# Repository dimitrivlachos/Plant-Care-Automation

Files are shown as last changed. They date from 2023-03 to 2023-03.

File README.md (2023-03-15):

# Plant Care Automation
ESP8266 microcontroller based, automated plant care project for ```CM3040 - Physical Computing and Internet of Things``` University of London.

To build out this system, I decided I would have a server-client type relationship between the controllers. The ```Base Station``` would be the server/host/controller of the entire system and it would serve multiple ```Plant Monitoring Stations```, which were the clients. I only built one example of each, but the general concept should be near infinitely scalable. These nodes communicate through REST-based HTTP requests, transferring JSON data as requested.

## Project design and demonstration video
IoT Demo Video (https://www.youtube.com/watch?v=c-YxRt0L1Ww)

## Nodes
The ```Base Station``` would monitor and display ambient environmental factors, as well as the water reservoir for the plants, checking in with each monitor node and issuing commands, such as to water the plant, turn on a light or open the greenhouse for fresh air. This node would be plugged into a mains power source and be somewhere prominent where it can display information.

The ```Plant Monitoring Station```, on the other hand, would be attached to each plant/greenhouse container. It would monitor the direct conditions affecting the plant, such as the soil moisture, temperature and humidity. It would also control the pump, servo and lights that water, open and illuminate the plant, based on commands issued from the base station.

---

# Breakdown of circuits
## Base Station

### Input / Sensors
* BMP280 - Temperature, humidity and barometric pressure sensor.
* BH1750 - Ambient light sensor.
* HCSR04 - Ultrasonic distance sensor.
* Push button - Used to manually trigger watering.

### Output / Actuators
* SSD1306 - 128x64 OLED display.
* Integrated LED - Used to indicate when the system is active on the network.

### JSON Data
The base station node sends JSON data in the following format:
```json
{
  "Content-Type": "application/json",
  "Status": 200,
  "Readings": {
    "temperature": 21.18000031,
    "humidity": 64.43847656,
    "pressure": 1017.714844,
    "lux": 49.16666412,
    "fill_percent": 100
  }
}
```

### Operation
The base station node constantly checks its sensors and updates its readings, displaying them on the OLED display. If an HTTP request is made to the base station, depending on the request, it will respond with either an HTML web dashboard or a JSON object containing its sensor readings.

The web page contains code that regularly sends an HTTP request to the base station, to get updated sensor readings in the form of a JSON. It then updates the web page with the new readings.

The physical push button is duplicated on the web page, this can be pressed to manually trigger watering. When the button is pressed, the base station will send an HTTP command to the plant monitoring stations to water the plants.

The base station also has a built-in LED that is used to indicate when the system is active on the network. It flashes three times when a request is made for the web page, and it flashes twice when a request is made for JSON data instead. It also flashes four times when initialising the BME280 sensor on startup.

The location of the text on the OLED display regularly shifts in order to prevent burn-in.

The ultrasonic distance sensor is used to check the water level in the reservoir. It is mounted above the water in the resevoir that each plant stations' pump draws from. This information can be checked on the web page.

The base station checks in with each of the plant monitoring stations regularly, it sends an HTTP request for a JSON file containing the status of each node.

It then processes the JSON data and decides whether to issue a command to the plant monitoring station. The commands are as follows:
1. If the pump is **not** running, it will check if the soil moisture is below a certain threshold. If it is, it will send an HTTP command to the plant monitoring station to water the plant.
2. If the lid (controlled by the servo) is **closed**, it will check if the temperature inside the greenhouse is too hot. If it is, it compares it with the outside, ambient temperature. If the greenhouse is hotter, it will send an HTTP command to the plant monitoring station to open the lid.
3. If the lid (controlled by the servo) is **open**, it will check if the temperature inside the greenhouse is too cold. If it is, it will send an HTTP command to the plant monitoring station to close the lid.
4. If the light is **off**, it will check if the ambient light is too low. If it is, it will send an HTTP command to the plant monitoring station to turn the plant light on.
5. If the light is **on**, it will check if the ambient light is adequate. If it is, it will send an HTTP command to the plant monitoring station to turn the plant light off.

### Circuit Diagram
* The **BME280** and **BH1750** sensors are connected to the ESP8266 via I2C, along with the **SSD1306** display. This is using the default I2C pins, SCL on pin D1 and SDA on pin D2.
* The **HCSR04** ultrasonic distance sensor is connected to the ESP8266 via the default pins, trigger on pin D6 and echo on pin D7.
* The push button is connected to pin D5 and has a pull-down resistor to ground.
* The integrated LED is internally connected to pin D4 (and the signal is inverted).

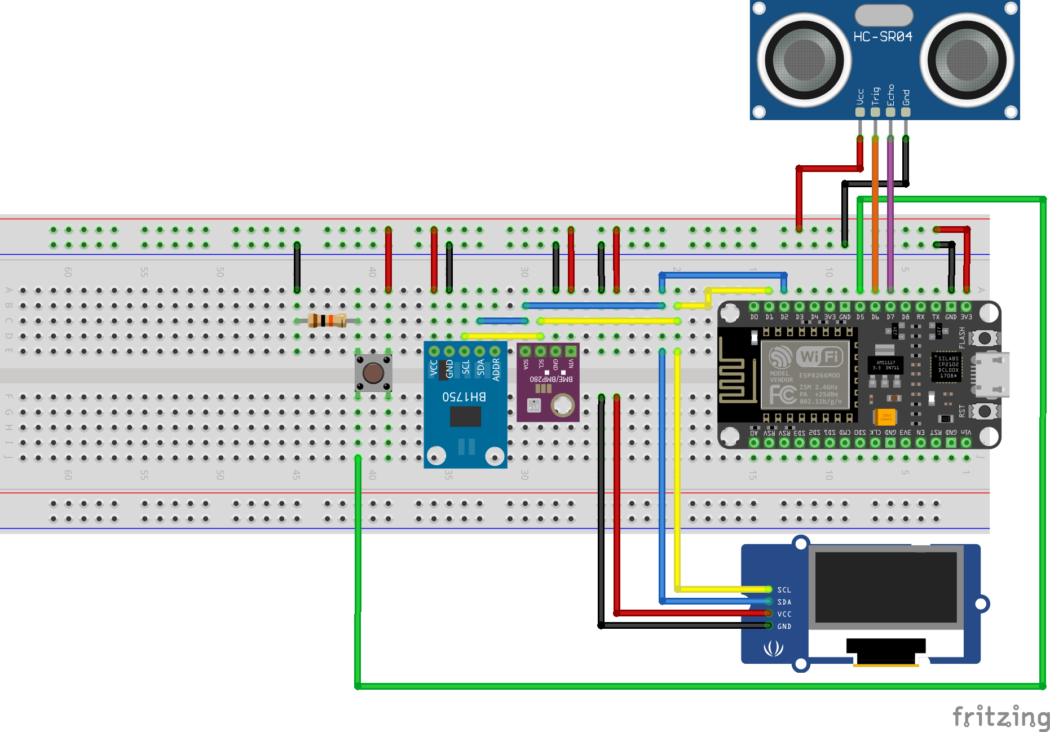
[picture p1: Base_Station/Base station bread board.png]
Base station breadboard diagram


### Web Interface
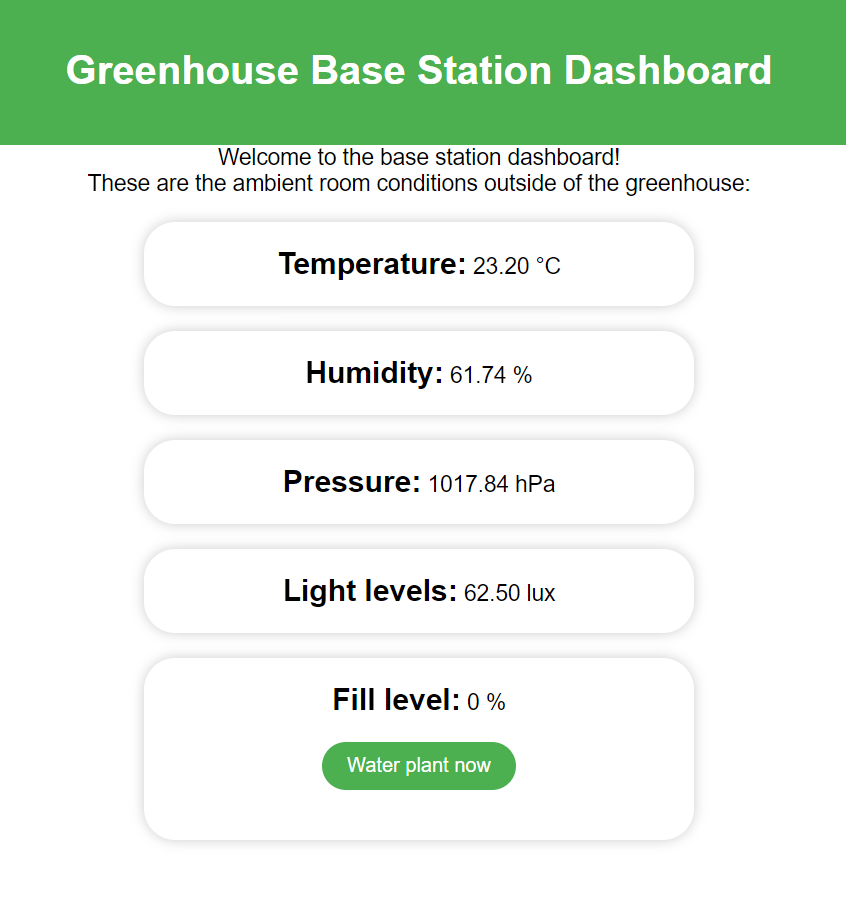
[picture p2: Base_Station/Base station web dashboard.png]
Base station web interface screenshot


## Plant Monitoring Station

### Input / Sensors
* DHT11 - Temperature and humidity sensor.
* Capacitive soil moisture sensor.

### Output / Actuators
* Servo - Used to open and close the lid of the greenhouse.
* Relay - Used to control the power to the pump.
* Pump - Used to water the plant.
* LED - Used to illuminate the plant.
* Integrated LED - Used to indicate when the system is active on the network.

### JSON Data
The plant monitoring station node sends JSON data in the following format:
```json
{
  "Content-Type": "application/json",
  "Status": 200,
  "Readings": {
    "soil_moisture_percent": 97,
    "temperature": 21,
    "humidity": 60
  },
  "States": {
    "servo_state": false,
    "pump_state": false,
    "light_state": true
  }
}
```

## Operation
The plant monitoring station node constantly checks its sensors and updates its readings. If an HTTP request is made to the plant monitoring station, depending on the request, it will respond with either an HTML web dashboard or a JSON object containing its sensor readings.

The web page contains code that regularly sends an HTTP request to the plant monitoring station, to get updated sensor readings in the form of a JSON. It then updates the web page with the new readings.

The web page includes a 'Water plant now' button, this can be pressed to manually trigger watering. When the button is pressed, the base station will run its ```water_plant()``` function manually, allowing users to trigger individual nodes to water.

The plant monitoring station also has a built-in LED that is used to indicate when the system is active on the network. It flashes three times when a request is made for the web page, and it flashes twice when a request is made for JSON data instead.

The plant monitoring station does not act on its own, it only responds to HTTP commands from the base station, such as:

* Request sensor readings - This is done by sending a JSON object containing the sensor readings.
* Request index page - This is done by sending an HTML web page.
* Water the plant - This is done by turning on the pump for a set amount of time before turning it off again.
* Open the lid - This is done by rotating the servo to a set angle.
* Close the lid - This is done by rotating the servo to its original angle.
* Turn the light on - This is done by turning on the LED pin. (For a more powerful LED, this can be replaced with a relay to control a mains powered light.)
* Turn the light off - This is done by turning off the LED pin.

### Circuit Diagram
* The **DHT11** sensor is connected to the ESP8266 via the D5 pin.
* The **capacitive soil moisture sensor** is connected to the ESP8266 via the A0 pin (This prevents us from being able to measure battery percentage).
* The **servo** is connected to the ESP8266 via the D6 pin.
* The **relay** (and **pump**) are connected to the ESP8266 via the D7 pin.
* The **LED** is connected to the ESP8266 via the D1 pin.

In this diagram, the entire circuit is powered by a battery pack. However, this is only representative of the solar power circuit intended to power it, as its exact operation is not important to this project. For the sake of environmental friendliness and ease of installation, these nodes are intended to be solar powered and contain a battery pack to store the energy.

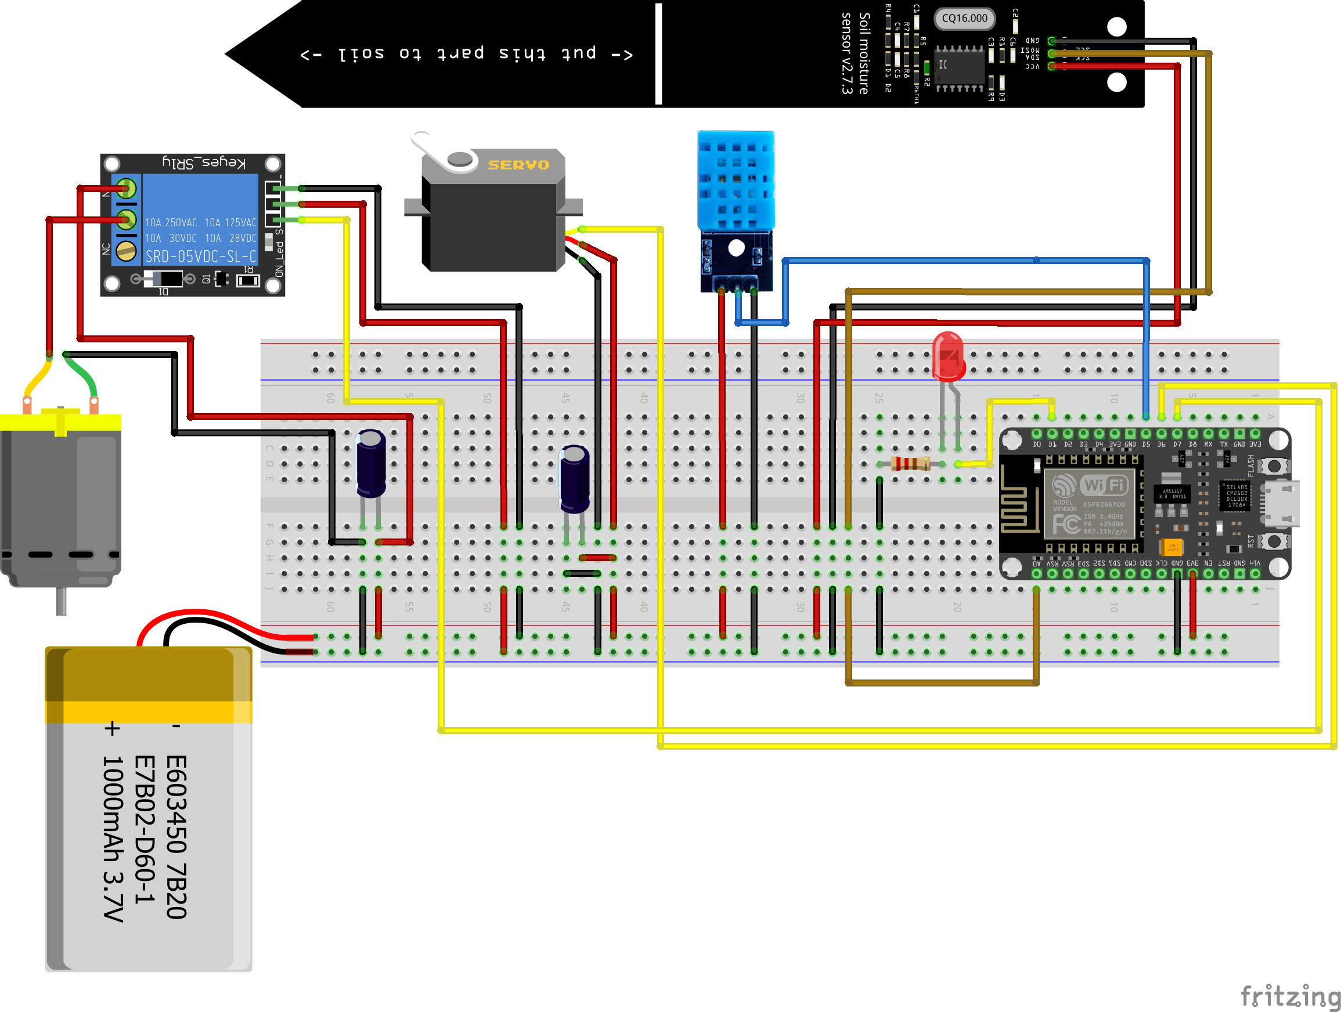
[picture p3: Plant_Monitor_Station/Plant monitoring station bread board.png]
Plant monitoring station breadboard diagram


### Web Interface
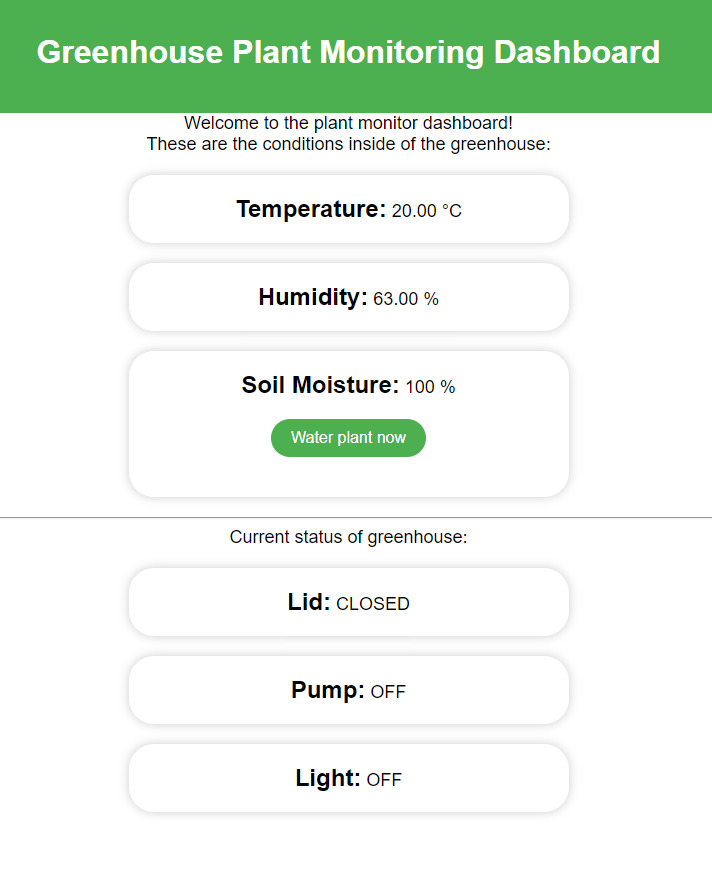
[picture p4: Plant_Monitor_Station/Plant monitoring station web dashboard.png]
Plant monitoring station web interface screenshot


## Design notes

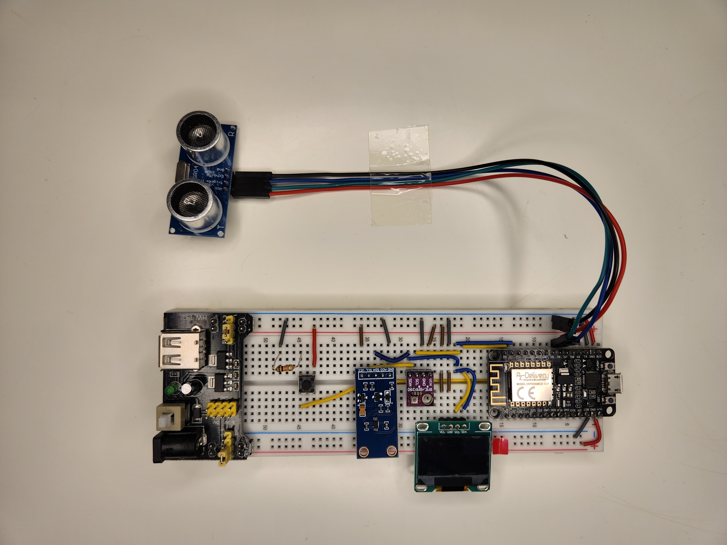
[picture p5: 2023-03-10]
Base_Station/Base station prototype breadboard.jpg

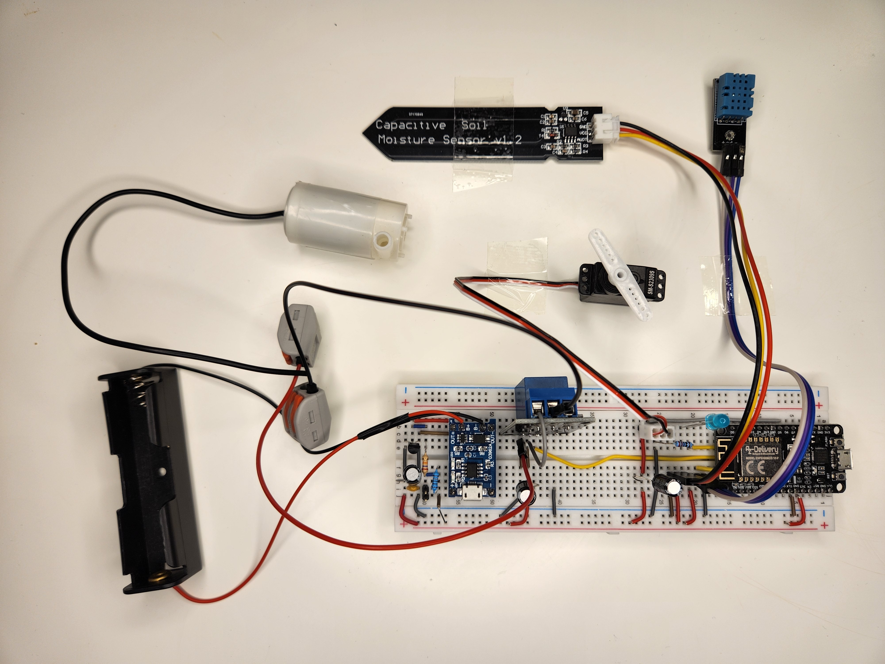
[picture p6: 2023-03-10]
Plant_Monitor_Station/Plant monitoring station prototype breadboard.jpg

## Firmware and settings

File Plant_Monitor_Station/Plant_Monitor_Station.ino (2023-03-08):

/*
 *  Code by:  Dimitrios Vlachos
 *            dimitri.j.vlachos@gmail.com
 *
 *  Adapted from:
 *            UoL Lectures
 *            https://randomnerdtutorials.com/esp8266-pinout-reference-gpios/
 *            https://makersportal.com/blog/2020/5/26/capacitive-soil-moisture-calibration-with-arduino
 *            https://randomnerdtutorials.com/esp8266-nodemcu-http-get-post-arduino/
 *            https://arduinojson.org/
 *
 */

#include <Adafruit_Sensor.h>
#include <Adafruit_BME280.h>
#include <Arduino_JSON.h>
#include "DHT.h"
#include <Servo.h>
#include <TaskScheduler.h>

/* * * * * * * * * * * * * * * */
#pragma region Networking
#include <ESP8266WiFi.h>
#include <ESP8266WebServer.h>
#include <ESP8266HTTPClient.h>
#include <ArduinoJson.h>

// For OTA
#include <WiFiUdp.h>
#include <ArduinoOTA.h>

// Allocate the JSON document
// Allows to allocated memory to the document dynamically.
DynamicJsonDocument doc(1024);

// Set the PORT for the web server
ESP8266WebServer server(80);

// The WiFi details
const char* ssid = "REPLACE_WITH_YOUR_SSID";
const char* password = "REPLACE_WITH_YOUR_PASSWORD";
#pragma endregion
/* * * * * * * * * * * * * * * */

Scheduler userScheduler;

/* * * * * * * * * * * * * * * */
// Function prototypes
/**
 * Updates global sensor reading variables with
 * new information from the sensors
 */
void updateReadings();
void blinkOn();
/*
 * blink the onboard LED
 *
 * @param blinks Number of times to blink the LED
 * @param interval Delay between blinks
 */
void blinkLED(int blinks, long interval = TASK_SECOND / 10);  // Prototype for default parameter values
void stopWatering();

/* * * * * * * * * * * * * * * */
// Create tasks
Task taskUpdateReadings(TASK_SECOND * 5, TASK_FOREVER, &updateReadings);
Task taskLedBlink(TASK_SECOND / 2, 4, &blinkOn);
Task taskStopWateringTimer(TASK_SECOND * 5, TASK_FOREVER, &stopWatering);

/* * * * * * * * * * * * * * * */
// Pin declarations
const int light_pin = D1;
const int led_pin = D4;
const int dht_pin = D5;
const int servo_pin = D6;
const int pump_pin = D7;
const int soil_pin = A0;

// Values to calibrate for soil moisture sensor
const int air_value = 620;
const int water_value = 310;

// Base node address
const String baseAddress = "http://192.168.0.201";

/* * * * * * * * * * * * * * * */
// Sensor declarations
// Initialise the components

DHT dht(dht_pin, DHT11);
Servo serv;

/* * * * * * * * * * * * * * * */
// Dynamic global variables

int soil_moisture_percent;
int temperature;
int humidity;

// Boolean to check open/close status of servo
bool isServoOpen = false;
bool isPumping = false;
bool light = false;

void setup() {
  // Start serial communication
  Serial.begin(115200);
  // Set the light relay pin mode
  pinMode(light_pin, OUTPUT);
  // Set led pin mode (integrated LED)
  pinMode(led_pin, OUTPUT);
  // Set pump pin mode
  pinMode(pump_pin, OUTPUT);

  // Initialise sensor
  dht.begin();
  // Initialise actuator
  serv.attach(servo_pin);
  // Populate initial sensor data
  updateReadings();

#pragma region WiFi Setup
  //Connect to the WiFi network
  WiFi.begin(ssid, password);

  // Wait for connection
  while (WiFi.status() != WL_CONNECTED) {
    delay(500);
    Serial.println("Waiting to connect...");
  }

#pragma region OTA Setup
  // Port defaults to 8266
  // ArduinoOTA.setPort(8266);

  // Hostname defaults to esp8266-[ChipID]
  ArduinoOTA.setHostname("Plant Monitor Station");

  // No authentication by default
  ArduinoOTA.setPassword("admin");

  // Password can be set with it's md5 value as well
  // MD5(admin) = 21232f297a57a5a743894a0e4a801fc3
  // ArduinoOTA.setPasswordHash("21232f297a57a5a743894a0e4a801fc3");

  ArduinoOTA.onStart([]() {
    String type;
    if (ArduinoOTA.getCommand() == U_FLASH) {
      type = "sketch";
    } else {  // U_FS
      type = "filesystem";
    }

    // NOTE: if updating FS this would be the place to unmount FS using FS.end()
    Serial.println("Start updating " + type);
  });
  ArduinoOTA.onEnd([]() {
    Serial.println("\nEnd");
  });
  ArduinoOTA.onProgress([](unsigned int progress, unsigned int total) {
    Serial.printf("Progress: %u%%\r", (progress / (total / 100)));
  });
  ArduinoOTA.onError([](ota_error_t error) {
    Serial.printf("Error[%u]: ", error);
    if (error == OTA_AUTH_ERROR) {
      Serial.println("Auth Failed");
    } else if (error == OTA_BEGIN_ERROR) {
      Serial.println("Begin Failed");
    } else if (error == OTA_CONNECT_ERROR) {
      Serial.println("Connect Failed");
    } else if (error == OTA_RECEIVE_ERROR) {
      Serial.println("Receive Failed");
    } else if (error == OTA_END_ERROR) {
      Serial.println("End Failed");
    }
  });
  ArduinoOTA.begin();
#pragma endregion

  //Print the board IP address
  Serial.print("IP address: ");
  Serial.println(WiFi.localIP());

  server.on("/", get_index);     // Get the index page on root route
  server.on("/json", get_json);  // Get the json data on the '/json' route
  server.on("/waterplant", water_plant); // Activate the watering function
  server.on("/setservo", setServo); // Allows for REST-based servo state setting
  server.on("/setlight", setLight); // Allows for REST-based light state setting

  server.begin();  //Start the server
  Serial.println("Server listening");
#pragma endregion

  // Async task setup
  userScheduler.addTask(taskUpdateReadings);
  userScheduler.addTask(taskLedBlink);
  userScheduler.addTask(taskStopWateringTimer);
  taskUpdateReadings.enable();

  // Initialise JSON object structure
  setupJSON();
}

void loop() {
  // Handle OTA events
  ArduinoOTA.handle();
  //Handling of incoming client requests
  server.handleClient();
  // Handling async tasks
  userScheduler.execute();
}

/**
 * Read data from the soil moisture sensor and use
 * the calibration to map the voltage to percentage
 */
int getSoilMoisture() {
  // Get voltage reading
  int soil_moisture_value = analogRead(soil_pin);
  // Convert into 'calibrated' percentage (need to calibrate)
  int percentageHumidity = map(soil_moisture_value, air_value, water_value, 100, 0);
  return percentageHumidity;
}

/*
 * Water plant function. This runs the pump in 5 second
 * intervals, pumping water into the plant pot as necessary.
 */
void water_plant() {
  Serial.println("Water plant request received");
  startWatering();
  server.send(200,"application/json",
  "{\"Content-Type\": \"application/json\",\"Status\": 200}");
}

/*
 * This function is called by the server upon receiving the
 * appropriate HTTP request. It pulls the state from the
 * HTTP arguments and sets the servo accordingly
 */
void setServo() {
  Serial.println("Set servo request received");
  bool state = getArgs();
  setServoState(state);
}

/*
 * This function is called by the server upon receiving the
 * appropriate HTTP request. It pulls the state from the
 * HTTP arguments and sets the light accordingly
 */
void setLight() {
  Serial.println("Set light request received");
  bool state = getArgs();
  setLightState(state);
}

/*
 * This function is called by the server upon receiving the
 * appropriate HTTP request.
 *
 * It sets the pump to on and activates a task that will
 * callback the stopWatering() function after 5 seconds.
 */
void startWatering() {
  digitalWrite(pump_pin, HIGH);
  isPumping = true;
  taskStopWateringTimer.enableDelayed(TASK_SECOND * 5);
}

/*
 * This function is called by the taskStopWateringTimer task.
 * After the set delay, this turns the pump off and disables
 * the task for use again later.
 */
void stopWatering() {
  digitalWrite(pump_pin, LOW);
  isPumping = false;
  taskStopWateringTimer.disable();
}

/*
 * This functions flips the servo motor between two positions
 * based on the 'state' requested. This opens and closes the
 * lid of the small greenhouse the servo is attached to.
 *
 * @param open Boolean for the state to set the lid to
 */
void setServoState(bool open) {
  if(open) {
    serv.write(180);
    isServoOpen = true;
  }
  else {
    serv.write(0);
    isServoOpen = false;
  }
}

/*
 * This functions turns the LED array on or offbased on the
 * 'state' requested. This provides light to the plants when
 * ambient lighting conditions are inadequate.
 *
 * @param on Boolean for the state to set the LED to
 */
void setLightState (bool on) {
  if(on) {
    digitalWrite(light_pin, HIGH);
    light = true;
  }
  else {
    digitalWrite(light_pin, LOW);
    light = false;
  }
}

/* * * * * * * * * * * * * * * * * * * * * * * * * * *
 * This region contains functions that get called by *
 * the task Scheduler, allowing for asynchronous     *
 * task execution without the need for using delay   *
 * functions. Check above to see how often each of   *
 * these tasks get pinged.                           *
 * * * * * * * * * * * * * * * * * * * * * * * * * * */
#pragma region Tasks
/**
 * Updates global sensor reading variables with
 * new information from the sensors
 */
void updateReadings() {
  soil_moisture_percent = constrain(getSoilMoisture(), 0, 100);
  temperature = dht.readTemperature();
  humidity = dht.readHumidity();
  /*
  // Debug
  Serial.print("Temp: ");
  Serial.println(temperature);
  Serial.print("Hum: ");
  Serial.println(humidity);
  Serial.print("Soil: ");
  Serial.println(soil_moisture_percent);
  */
}
#pragma endregion

/* * * * * * * * * * * * * * * * * * * * * * * * * * *
 * This region contains functions necessary for the  *
 * webserver to run, enabling the dashboard and REST *
 * requests to be made.                              *
 * * * * * * * * * * * * * * * * * * * * * * * * * * */
#pragma region Network code
// Web dashboard HTML
#pragma region HTML
/*
 * Here we create the static web dashboard for this controller.
 * By using the variable modifier PROGMEM, we store this code
 * in the flash memory instead of into SRAM. This frees up a
 * considerable amount of RAM that would otherwise just hold
 * onto a static string.
 */
const char index_html[] PROGMEM = R"rawliteral(
<!DOCTYPE html>
<html>
  <head>
    <meta name="viewport" content="width=device-width, initial-scale=1.0">
    <title>Greenhouse Plant Monitoring Dashboard</title>
    <style>
      body {
        font-family: Arial, sans-serif;
        margin: 0;
        padding: 0;
      }
      header {
        background-color: #4CAF50;
        color: white;
        padding: 20px;
        text-align: center;
      }
      .card {
        border-radius: 25px;
        box-shadow: 0 0 10px rgba(0, 0, 0, 0.2);
        padding: 20px;
        text-align: center;
        margin: 20px auto;
        max-width: 400px;
      }
      p {
        margin: 0;
        font-size: 18px;
        text-align: center;
      }
      strong {
        font-size: 24px;
      }
      button {
        margin: 20px;
        padding: 10px 20px;
        font-size: 16px;
        border-radius: 25px;
        background-color: #4CAF50;
        color: white;
        border: none;
        cursor: pointer;
      }
    </style>
  </head>
  <body>
    <header>
      <h1>Greenhouse Plant Monitoring Dashboard</h1>
    </header>
    <div>
      <p></p>
      <p>Welcome to the plant monitor dashboard!</p>
      <p>These are the conditions inside of the greenhouse:</p>
    </div>
    
    <section id="readings">
      <div class="card">
        <p><strong>Temperature:</strong> <span id="temperature"></span> &degC</p>
      </div>
      <div class="card">
        <p><strong>Humidity:</strong> <span id="humidity"></span> %</p>
      </div>
      <div class="card">
        <p><strong>Soil Moisture:</strong> <span id="soil-moisture"></span> %</p>
        <button onclick="waterPlant()">Water plant now</button>
      </div>
    </section>

    <hr>
    <p>Current status of greenhouse:</p>
    
    <section id="states">
      <div class="card">
        <p><strong>Lid:</strong> <span id="servo-state"></span></p>
      </div>
      <div class="card">
        <p><strong>Pump:</strong> <span id="pump-state"></span></p>
      </div>
      <div class="card">
        <p><strong>Light:</strong> <span id="light-state"></span></p>
      </div>
    </section>

    <script>
      function updateValues() {
        const url = window.location.href + 'json';

        fetch(url)
          .then(response => response.json())
          .then(data => {
            const temperature = data.Readings.temperature;
            const humidity = data.Readings.humidity;
            const soil_moisture = data.Readings.soil_moisture_percent;
            const servo_state = data.States.servo_state;
            const pump_state = data.States.pump_state;
            const light_state = data.States.light_state;

            document.getElementById('temperature').innerHTML = temperature.toFixed(2);
            document.getElementById('humidity').innerHTML = humidity.toFixed(2);
            document.getElementById('soil-moisture').innerHTML = soil_moisture;
            document.getElementById('servo-state').innerHTML = servo_state ? "OPEN" : "CLOSED";
            document.getElementById('pump-state').innerHTML = pump_state ? "ON" : "OFF";
            document.getElementById('light-state').innerHTML = light_state ? "ON" : "OFF";
          })
          .catch(error => {
            console.error('Error fetching data:', error);
          });
      }

      function waterPlant() {
        const url = window.location.href + 'waterplant';

        fetch(url, { method: 'POST' })
          .then(response => {
            if (response.ok) {
              console.log('Plant watered successfully!');
            } else {
              console.error('Error watering plant:', response.statusText);
            }
          })
          .catch(error => {
            console.error('Error watering plant:', error);
          });
      }
      
      updateValues();
      setInterval(updateValues, 5000);
    </script>
  </body>
</html>
)rawliteral";
#pragma endregion

// Function called to send webpage to client
void get_index() {
  // Blink LED for visual queue
  blinkLED(3);
  //Send the webpage
  server.send(200, "text/html", index_html);
}

// Function called to send JSON data to client
void get_json() {
  // Blink LED for visual queue
  blinkLED(2);
  // Create JSON data
  updateJSON();
  // Make JSON data ready for the http request
  String jsonStr;
  serializeJsonPretty(doc, jsonStr);
  // Send the JSON data
  server.send(200, "application/json", jsonStr);
}

/*
 * Update JSON doc with most up-to-date
 * readings from the sensors.
 */
void updateJSON() {
  doc["Readings"]["soil_moisture_percent"] = soil_moisture_percent;
  doc["Readings"]["temperature"] = temperature;
  doc["Readings"]["humidity"] = humidity;

  doc["States"]["servo_state"] = isServoOpen;
  doc["States"]["pump_state"] = isPumping;
  doc["States"]["light_state"] = light;
}

/*
 * Initialise JSON doc file structure and
 * populate the fields with initial
 * sensor values.
 */
void setupJSON() {
  // Add JSON request data
  doc["Content-Type"] = "application/json";
  doc["Status"] = 200;

  // Add sensor readings to JSON object data
  JsonObject sensorReadings = doc.createNestedObject("Readings");
  sensorReadings["soil_moisture_percent"] = soil_moisture_percent;
  sensorReadings["temperature"] = temperature;
  sensorReadings["humidity"] = humidity;

  // Add actuator states to JSON object data
  JsonObject actuatorStates = doc.createNestedObject("States");
  actuatorStates["servo_state"] = isServoOpen;
  actuatorStates["pump_state"] = isPumping;
  actuatorStates["light_state"] = light;
}

/*
 * This function pulls the parameters out of the previously
 * received HTTP request. These parameters will be on of
 * two states, the function returns a bool accordingly.
 *
 * @returns state State requested from parameters
 */
bool getArgs () {
  int query = 0;
  bool state = false;

  // Check the query string
  if (server.arg("state") != "") {  // Parameter found
    // Parse the value from the query
    query = server.arg("state").toInt();
    // Update the minimum distance value
    state = query;
  }
  server.send(200,"application/json",
  "{\"Content-Type\": \"application/json\",\"Status\": 200}");
  return state;
}
#pragma endregion

/* * * * * * * * * * * * * * * * * * * * * * * * * * *
 * Task based LED blinking functionality.            *
 * This works by using a Task to callback on         *
 * alternating 'on-off' functions.                   *
 * * * * * * * * * * * * * * * * * * * * * * * * * * */
#pragma region LED Blink functions
/*
 * blink the onboard LED
 *
 * @param blinks Number of times to blink the LED
 * @param interval Delay between blinks
 */
void blinkLED(int blinks, long interval) {
  taskLedBlink.setInterval(interval);
  taskLedBlink.setIterations(blinks * 2);  // Double the iterations as on->off->on is two cycles, not one
  taskLedBlink.enable();
}

// Turns LED on and changes task callback to turn off on next iteration
void blinkOn() {
  LEDOn();
  taskLedBlink.setCallback(&blinkOff);

  if (taskLedBlink.isLastIteration()) {
    LEDOff();
  }
}

// Turns LED off and changes task callback to turn on on next iteration
void blinkOff() {
  LEDOff();
  taskLedBlink.setCallback(&blinkOn);

  if (taskLedBlink.isLastIteration()) {
    LEDOff();
  }
}

// Writes LED state to pin
inline void LEDOn() {
  digitalWrite(led_pin, HIGH);
}

// Writes LED state to pin
inline void LEDOff() {
  digitalWrite(led_pin, LOW);
}
#pragma endregion

/* * * * * * * * * * * * * * * * * * * * * * * * * * *
 * Functions for battery monitoring. Currently       *
 * unused due to the lack of available pins.         *
 * * * * * * * * * * * * * * * * * * * * * * * * * * */
#pragma region Battery code

/*
 * Checks the battery voltage using a voltage divider.
 * It then converts that voltage into a percent value.
 *
 * @return batteryLevel Percent of battery left
 */
// int checkBattery() {
//   float batteryLevel = map(analogRead(A0), 0.0f, 4095.0f, 0, 100);
//   Serial.println(batteryLevel);
//   return batteryLevel;
// }
#pragma endregion

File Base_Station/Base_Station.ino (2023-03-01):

/*
 *  Code by:  Dimitrios Vlachos
 *            dimitri.j.vlachos@gmail.com
 *
 *  Adapted from:
 *            UoL Lectures
 *            https://randomnerdtutorials.com/esp8266-pinout-reference-gpios/
 *            https://randomnerdtutorials.com/esp8266-nodemcu-http-get-post-arduino/
 *            https://randomnerdtutorials.com/esp8266-0-96-inch-oled-display-with-arduino-ide/
 *            https://arduinojson.org/
 *
 */

#include <Arduino_JSON.h>
#include <Adafruit_Sensor.h>
#include <Adafruit_BME280.h>
#include <Wire.h>
#include <BH1750.h>
#include <Adafruit_GFX.h>
#include <Adafruit_SSD1306.h>
#include <TaskScheduler.h>

/* * * * * * * * * * * * * * * */
#pragma region Networking
#include <ESP8266WiFi.h>
#include <ESP8266WebServer.h>
#include <ESP8266HTTPClient.h>
#include <ArduinoJson.h>

// For OTA
#include <WiFiUdp.h>
#include <ArduinoOTA.h>

// Allocate the JSON document
// Allows to allocated memory to the document dynamically.
DynamicJsonDocument doc(1024);

// Set the PORT for the web server
ESP8266WebServer server(80);

// The WiFi details
const char* ssid = "REPLACE_WITH_YOUR_SSID";
const char* password = "REPLACE_WITH_YOUR_PASSWORD";
#pragma endregion
/* * * * * * * * * * * * * * * */

#define SCREEN_WIDTH 128  // OLED display width, in pixels
#define SCREEN_HEIGHT 64  // OLED display height, in pixels

Scheduler userScheduler;

/* * * * * * * * * * * * * * * */
// Function prototypes
/**
 * Updates global sensor reading variables with
 * new information from the sensors
 */
void updateReadings();
void updateDisplay();
void oledSaver();
void blinkOn();
/*
 * blink the onboard LED
 *
 * @param blinks Number of times to blink the LED
 * @param interval Delay between blinks
 */
void blinkLED(int blinks, long interval = TASK_SECOND / 10);  // Prototype for default parameter values
void getMonitorReadings();
void resetButtonDebounce();
void sendState(String command, int state = -1);

/* * * * * * * * * * * * * * * */
//Create tasks
Task taskUpdateReadings(TASK_SECOND * 1, TASK_FOREVER, &updateReadings);
Task taskUpdateDisplay(TASK_SECOND * 1, TASK_FOREVER, &updateDisplay);
Task taskOledSaver(TASK_MINUTE * 5, TASK_FOREVER, &oledSaver);
Task taskLedBlink(TASK_SECOND / 2, 4, &blinkOn);
Task taskCheckMonitor(TASK_SECOND * 10, TASK_FOREVER, &getMonitorReadings);
Task taskDebounceReset(TASK_SECOND * 1, TASK_FOREVER, &resetButtonDebounce);

/* * * * * * * * * * * * * * * */
// Pin declarations
const int led_pin = D4;
const int button = D5;

// Pins for ultrasonic sensor
const int trig_pin = D6;
const int echo_pin = D7;

// Monitor node address
const String monitorAddress = "http://192.168.0.202";

/* * * * * * * * * * * * * * * */
// Sensor declarations

// BME object on the default I2C pins
Adafruit_BME280 bme;
// BH1750 object on the default I2C pins
BH1750 lightMeter;
// Declaration for an SSD1306 display connected to I2C (SDA, SCL pins)
Adafruit_SSD1306 display(SCREEN_WIDTH, SCREEN_HEIGHT, &Wire, -1);

/* * * * * * * * * * * * * * * */
// Dynamic global variables

// Text positions - see @oledSaver()
int screen_x;
int screen_y;

// Sensor readings
float temperature;
float humidity;
float pressure;
float lux;
int fill_percent;

// Flag for software debouncing
bool debouncer = false;

// Own IP address
String IP;

/* * * * * * * * * * * * * * * */

void setup() {
  // Start serial communication
  Serial.begin(115200);
  // Set led pin mode (integrated LED)
  pinMode(led_pin, OUTPUT);
  // Set the button pin mode
  pinMode(button, INPUT);
  // Set pins for distance sensor
  pinMode(trig_pin, OUTPUT);  // Sets the trigPin as an Output
  pinMode(echo_pin, INPUT);   // Sets the echoPin as an Input

  // Initialise onboard sensors
  initBME();
  lightMeter.begin();

  // Populate initial sensor data
  updateReadings();

  // Initialise text position
  oledSaver();

  // Initialise display
  if (!display.begin(SSD1306_SWITCHCAPVCC, 0x3C)) {
    Serial.println("SSD1306 allocation failed");
    for (;;)
      ;  // Don't proceed, loop forever
  }

  delay(2000);
  display.clearDisplay();

  #pragma region WiFi Setup
  //Connect to the WiFi network
  WiFi.begin(ssid, password);

  // Wait for connection
  while (WiFi.status() != WL_CONNECTED) {
    delay(500);
    Serial.println("Waiting to connect...");
  }

  #pragma region OTA Setup
  // Port defaults to 8266
  // ArduinoOTA.setPort(8266);

  // Hostname defaults to esp8266-[ChipID]
  ArduinoOTA.setHostname("Base Station");

  // No authentication by default
  ArduinoOTA.setPassword("admin");

  // Password can be set with it's md5 value as well
  // MD5(admin) = 21232f297a57a5a743894a0e4a801fc3
  // ArduinoOTA.setPasswordHash("21232f297a57a5a743894a0e4a801fc3");

  ArduinoOTA.onStart([]() {
    String type;
    if (ArduinoOTA.getCommand() == U_FLASH) {
      type = "sketch";
    } else {  // U_FS
      type = "filesystem";
    }

    // NOTE: if updating FS this would be the place to unmount FS using FS.end()
    Serial.println("Start updating " + type);
  });
  ArduinoOTA.onEnd([]() {
    Serial.println("\nEnd");
  });
  ArduinoOTA.onProgress([](unsigned int progress, unsigned int total) {
    Serial.printf("Progress: %u%%\r", (progress / (total / 100)));
  });
  ArduinoOTA.onError([](ota_error_t error) {
    Serial.printf("Error[%u]: ", error);
    if (error == OTA_AUTH_ERROR) {
      Serial.println("Auth Failed");
    } else if (error == OTA_BEGIN_ERROR) {
      Serial.println("Begin Failed");
    } else if (error == OTA_CONNECT_ERROR) {
      Serial.println("Connect Failed");
    } else if (error == OTA_RECEIVE_ERROR) {
      Serial.println("Receive Failed");
    } else if (error == OTA_END_ERROR) {
      Serial.println("End Failed");
    }
  });
  ArduinoOTA.begin();
  #pragma endregion

  //Print the board IP address
  Serial.print("IP address: ");
  IP = WiFi.localIP().toString();
  Serial.println(IP);

  server.on("/", get_index);     // Get the index page on root route
  server.on("/json", get_json);  // Get the json data on the '/json' route
  server.on("/waterplant", sendWaterCommand); // Activates te sendWaterCommand to send to the monitor node

  server.begin();  //Start the server
  Serial.println("Server listening");
  #pragma endregion

  // Async task setup
  userScheduler.addTask(taskUpdateReadings);
  userScheduler.addTask(taskUpdateDisplay);
  userScheduler.addTask(taskOledSaver);
  userScheduler.addTask(taskLedBlink);
  userScheduler.addTask(taskCheckMonitor);
  userScheduler.addTask(taskDebounceReset);
  taskUpdateReadings.enable();
  taskUpdateDisplay.enable();
  taskOledSaver.enable();
  taskCheckMonitor.enable();

  // Initialise JSON object structure
  setupJSON();
}

void loop() {
  // Handle OTA events
  ArduinoOTA.handle();
  // Handling of incoming client requests
  server.handleClient();
  // Handling async tasks
  userScheduler.execute();
  // Check the button
  checkButton();
}
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

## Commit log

2023-02-19 Uploaded code to repository
    Uploaded current mesh-based system into the repository
    [Plant monitoring station.fzz]
2023-02-23 Added LED blinking
    Added blink function into network requests to make their operation more visible.
2023-03-01 Fixed button name
2023-03-01 Added fritzing circuit diagrams
    Added circuit diagrams of both circuits
    [Base station.fzz, Plant monitoring station.fzz]
2023-03-02 Name refactoring
    [Base station.fzz, Plant monitoring station.fzz]
2023-03-02 Fixed web dash HTML
    [Plant_Monitor_Station.ino]
2023-03-10 Added images of actual circuits
